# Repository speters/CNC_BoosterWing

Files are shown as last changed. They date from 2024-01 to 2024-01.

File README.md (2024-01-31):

# grblHAL BoosterWing

A breakout board for the Texas Instruments EK-TM4C1294XL Launchpad running the [grblHAL TM4C1294](https://github.com/grblHAL/TM4C1294) firmware by [Terje Io](https://github.com/terjeio).

This is a Frankenstein style child of [GRBLHAL2000](https://github.com/Expatria-Technologies/grblhal_2000_PrintNC) and 
[CNC_Boosterpack](https://github.com/terjeio/CNC_Boosterpack).

There were two objectives for this:
  1. follow known-working proven schematics - no questions asked
  2. keep it manufacturable by JLCPCB with the least costs for extended parts

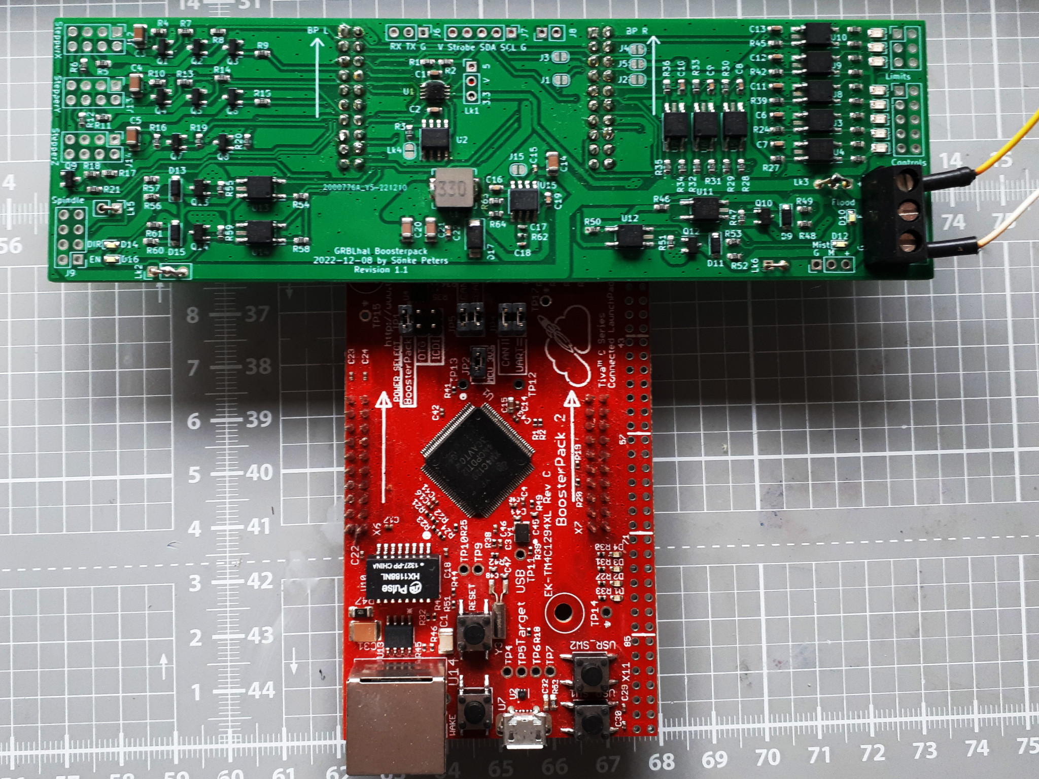
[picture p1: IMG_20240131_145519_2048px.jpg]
photo of BoosterWing with TM4C1294 board


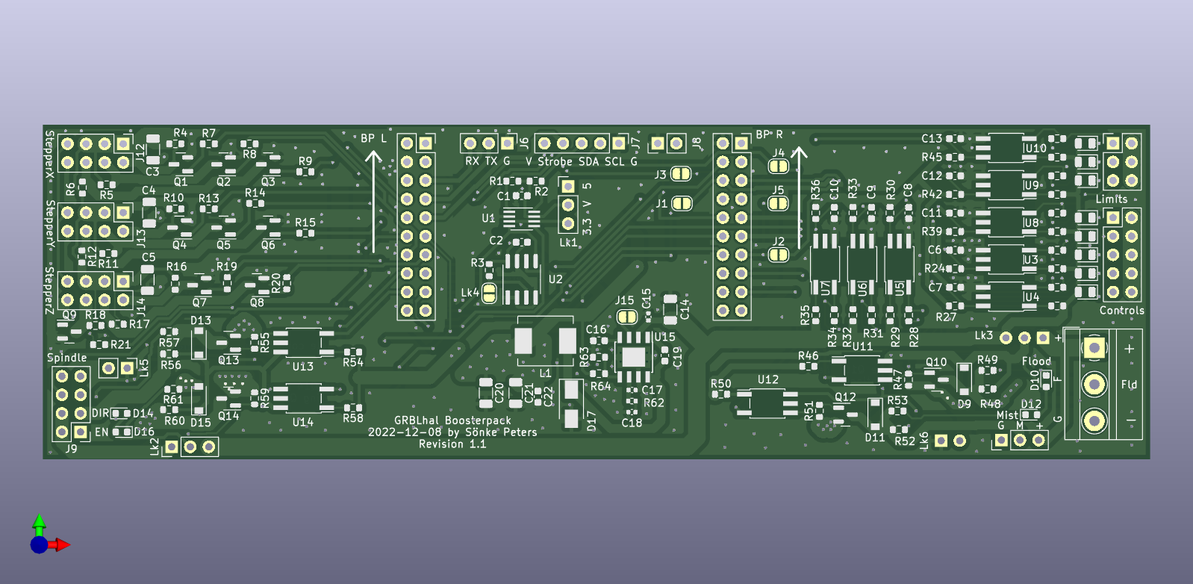
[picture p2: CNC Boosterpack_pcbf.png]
PCB front


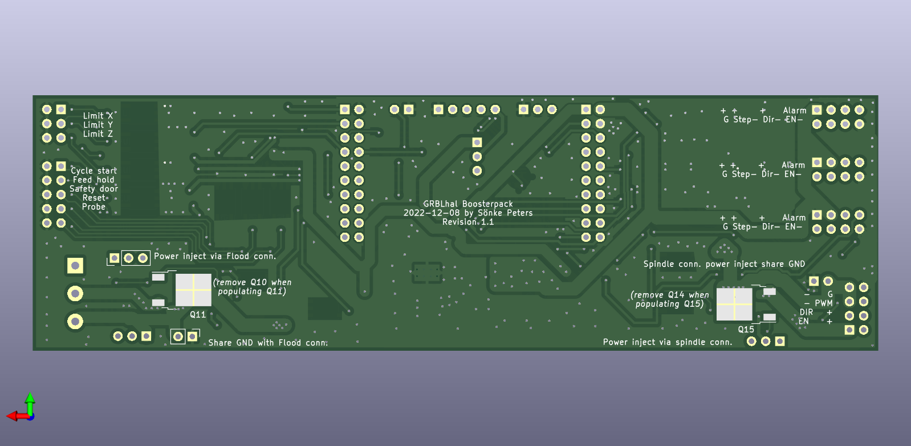
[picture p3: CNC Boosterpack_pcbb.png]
PCB back


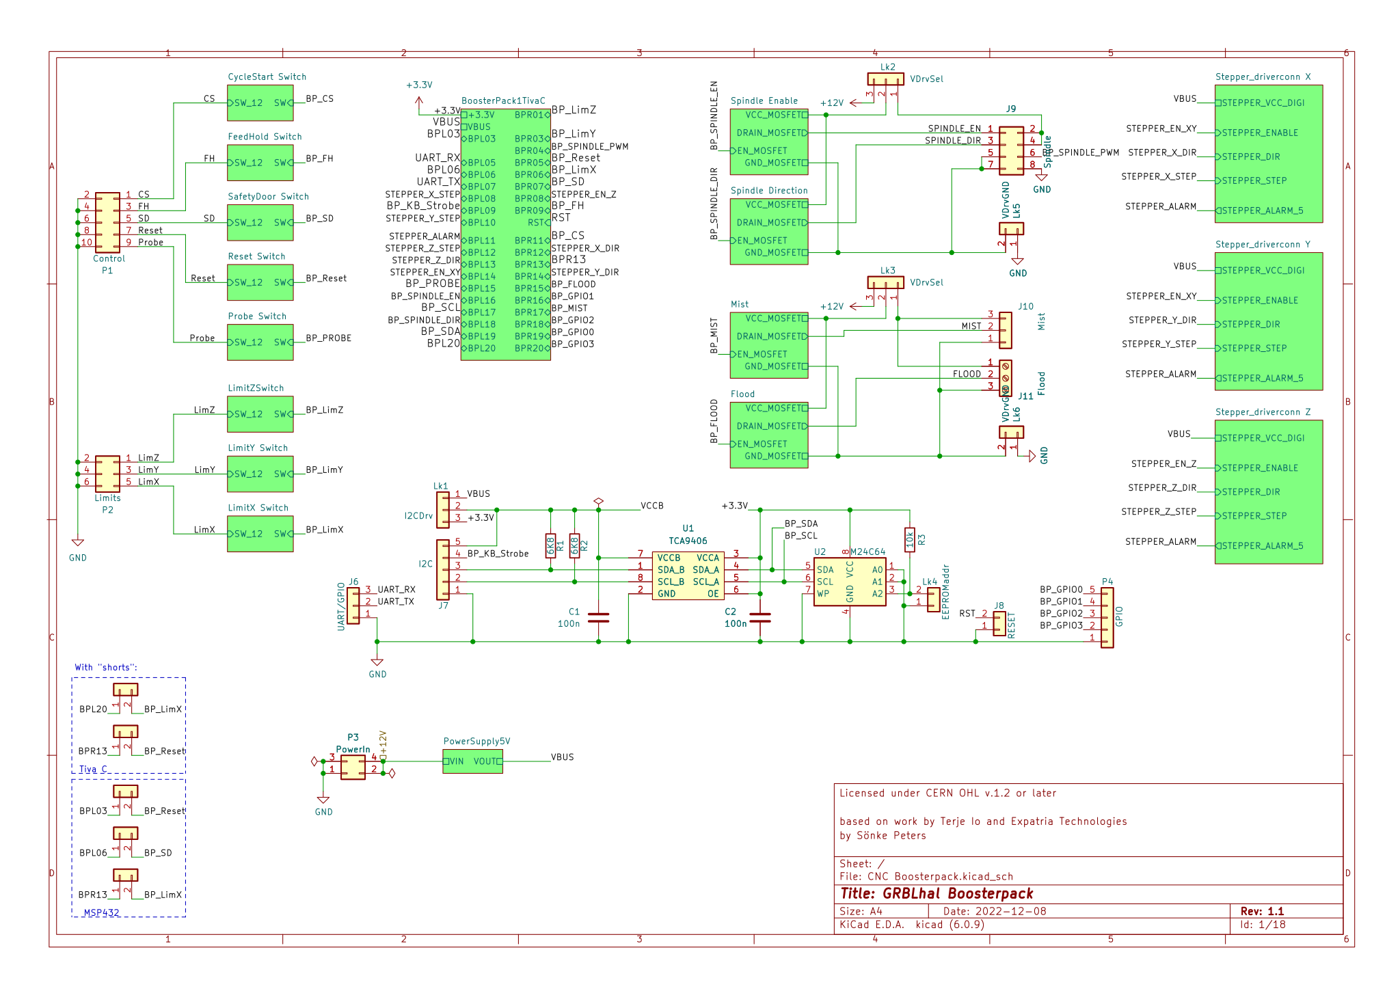
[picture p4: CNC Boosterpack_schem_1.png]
Schematics


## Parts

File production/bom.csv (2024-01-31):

Designator | Footprint | Quantity | Value | LCSC Part #
C1, C10, C11, C12, C13, C19, C2, C22, C6, C7, C8, C9 | C_0603_1608Metric | 12 | 100n | C14663
C14 | C_1206_3216Metric | 1 | 10u
C15 | C_0402_1005Metric | 1 | 10n
C16 | C_0603_1608Metric | 1 | 8.2n | C27920
C17 | C_0402_1005Metric | 1 | 10p | C32949
C18 | C_0402_1005Metric | 1 | 6.8n | C1542
C20, C21 | C_1206_3216Metric | 2 | 22u
C3, C4, C5 | C_1206_3216Metric | 3 | 22uF 10V | C5672
D1, D2, D3, D4, D5, D6, D7, D8 | LED_0805_2012Metric | 8 | LED y | C2296
D10, D12, D14, D16 | LED_0603_1608Metric | 4 | LED wt | C2290
D11, D13, D15, D9 | D_SOD-123 | 4 | B5819W SL | C8598
D17 | D_SMA | 1 | SS54
J1, J2, J3, J4, J5 | SolderJumper-2_P1.3mm_Open_RoundedPad1.0x1.5mm | 5 | 0
J10 | PinHeader_1x03_P2.54mm_Vertical | 1 | Mist
J11 | TerminalBlock_MetzConnect_Type011_RT05503HBWC_1x03_P5.00mm_Horizontal | 1 | Flood
J12, J13, J14 | PinHeader_2x04_P2.54mm_Vertical | 3 | StepperDrv
J15 | SolderJumper-2_P1.3mm_Open_RoundedPad1.0x1.5mm | 1 | 5V off
J6 | PinHeader_1x03_P2.54mm_Vertical | 1 | UART/GPIO
J7 | PinHeader_1x05_P2.54mm_Vertical | 1 | I2C
J8 | PinHeader_1x02_P2.54mm_Vertical | 1 | RESET
J9 | PinHeader_2x04_P2.54mm_Vertical | 1 | Spindle
L1 | L_Neosid_SM-PIC0602H | 1 | 33uH | C329385
Lk1 | PinHeader_1x03_P2.54mm_Vertical | 1 | I2CDrv
Lk2, Lk3 | PinHeader_1x03_P2.54mm_Vertical | 2 | VDrvSel
Lk4 | SolderJumper-2_P1.3mm_Open_RoundedPad1.0x1.5mm | 1 | EEPROMaddr
Lk5, Lk6 | PinHeader_1x02_P2.54mm_Vertical | 2 | VDrvGND
P1 | PinHeader_2x05_P2.54mm_Vertical | 1 | Control
P2 | PinHeader_2x03_P2.54mm_Vertical | 1 | Limits
P5 | PinSocket_2x10_P2.54mm_Vertical | 1 | BPConnL
P6 | PinSocket_2x10_P2.54mm_Vertical | 1 | BPConnR
Q1, Q2, Q3, Q4, Q5, Q6, Q7, Q8, Q9 | SOT-23 | 9 | MMBT5551 | C2145
Q10, Q12, Q13, Q14 | SOT-23 | 4 | AO3400A | C20917
R1, R2 | R_0603_1608Metric | 2 | 6K8 | C23212
R10, R11, R12, R16, R17, R18, R22, R25, R28, R31, R34, R37, R4, R40, R43, R5, R6 | R_0603_1608Metric | 17 | 4k7 | C23162
R13, R14, R15, R19, R20, R21, R23, R26, R29, R32, R35, R38, R41, R44, R7, R8, R9 | R_0603_1608Metric | 17 | 2k2 | C4190
R24, R27, R3, R30, R33, R36, R39, R42, R45, R63 | R_0603_1608Metric | 10 | 10k | C25804
R46, R50, R54, R58 | R_0603_1608Metric | 4 | 510 | C23193
R47, R51, R55, R59 | R_0603_1608Metric | 4 | 1k | C21190
R48, R49, R52, R53, R56, R57, R60, R61 | R_0603_1608Metric | 8 | 4,7k | C23162
R62 | R_0402_1005Metric | 1 | 51k | C25794
R64 | R_0603_1608Metric | 1 | 2k | C22975
U1 | SSOP-8_2.95x2.8mm_P0.65mm | 1 | TCA9406 | C337496
U10, U11, U12, U13, U14, U3, U4, U5, U6, U7, U8, U9 | SO-5_4.4x3.6mm_P1.27mm_fake | 12 | EL357N(B) | C6649
U15 | TI_SO-PowerPAD-8_ThermalVias | 1 | TPS54331DR | C9865
U2 | SOIC-8_3.9x4.9mm_P1.27mm | 1 | M24C64 | C79988

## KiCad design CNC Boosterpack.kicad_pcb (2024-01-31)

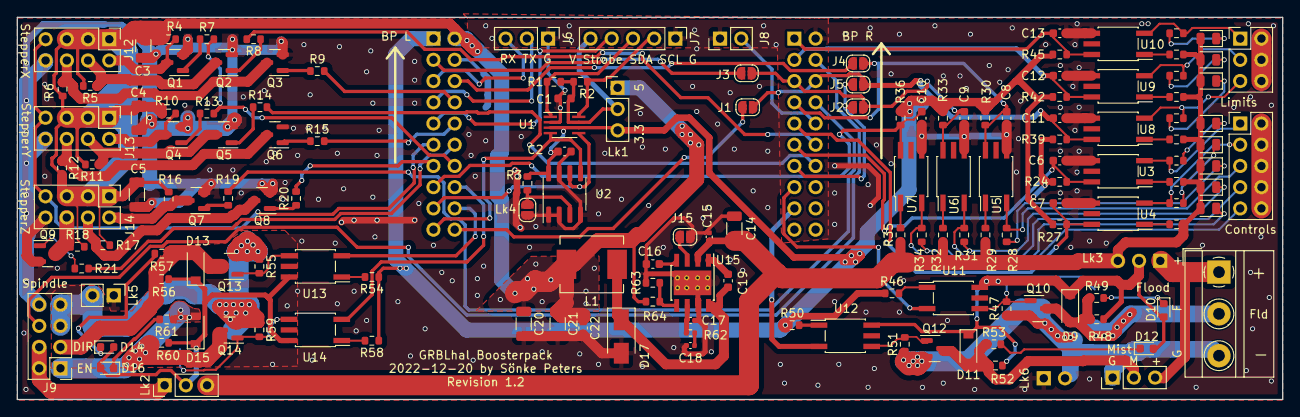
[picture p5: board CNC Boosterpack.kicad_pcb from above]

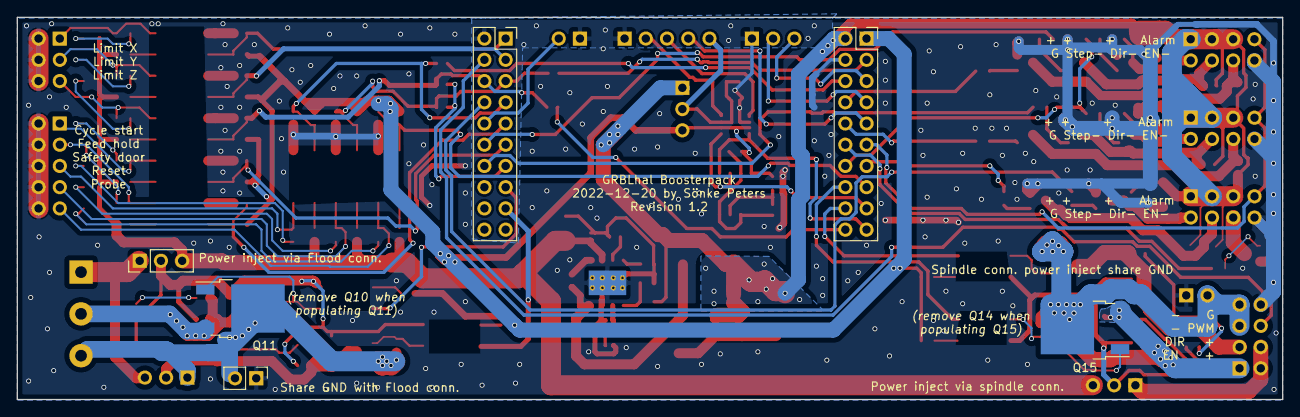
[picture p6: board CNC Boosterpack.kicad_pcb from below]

Board: 2 copper layers, 151.4 x 45.7 mm, 159 parts (6 on the bottom side), 111 nets.

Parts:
C1, C2, C6, C7, C8, C9, C10, C11, C12, C13, C19, C22: 100n; C_0603_1608Metric
C3, C4, C5: 22uF 10V; C_1206_3216Metric
C14: 10u; C_1206_3216Metric
C15: 10n; C_0402_1005Metric
C16: 8.2n; C_0603_1608Metric
C17: 10p; C_0402_1005Metric
C18: 6.8n; C_0402_1005Metric
C20, C21: 22u; C_1206_3216Metric
D1, D2, D3, D4, D5, D6, D7, D8: LED y; LED_0805_2012Metric
D9, D11, D13, D15: B5819W SL; D_SOD-123
D10, D12, D14, D16: LED wt; LED_0603_1608Metric
D17: SS54; D_SMA
J1, J2, J3, J4, J5: 0; SolderJumper-2_P1.3mm_Open_RoundedPad1.0x1.5mm
J6: UART/GPIO; PinHeader_1x03_P2.54mm_Vertical
J7: I2C; PinHeader_1x05_P2.54mm_Vertical
J8: RESET; PinHeader_1x02_P2.54mm_Vertical
J9: Spindle; PinHeader_2x04_P2.54mm_Vertical
J10: Mist; PinHeader_1x03_P2.54mm_Vertical
J11: Flood; TerminalBlock_MetzConnect_Type011_RT05503HBWC_1x03_P5.00mm_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
J12, J13, J14: StepperDrv; PinHeader_2x04_P2.54mm_Vertical
J15: 5V off; SolderJumper-2_P1.3mm_Open_RoundedPad1.0x1.5mm
L1: 33uH; L_Neosid_SM-PIC0602H
Lk1: I2CDrv; PinHeader_1x03_P2.54mm_Vertical
Lk2, Lk3: VDrvSel; PinHeader_1x03_P2.54mm_Vertical
Lk4: EEPROMaddr; SolderJumper-2_P1.3mm_Open_RoundedPad1.0x1.5mm
Lk5, Lk6: VDrvGND; PinHeader_1x02_P2.54mm_Vertical
P1: Control; PinHeader_2x05_P2.54mm_Vertical
P2: Limits; PinHeader_2x03_P2.54mm_Vertical
P5: BPConnL; PinSocket_2x10_P2.54mm_Vertical
P6: BPConnR; PinSocket_2x10_P2.54mm_Vertical
Q1, Q2, Q3, Q4, Q5, Q6, Q7, Q8, Q9: MMBT5551; SOT-23
Q10, Q12, Q13, Q14: AO3400A; SOT-23
Q11, Q15: HSU3016; TO-252-2
R1, R2: 6K8; R_0603_1608Metric
R3, R24, R27, R30, R33, R36, R39, R42, R45, R63: 10k; R_0603_1608Metric
R4, R5, R6, R10, R11, R12, R16, R17, R18, R22, R25, R28, R31, R34, R37, R40, R43: 4k7; R_0603_1608Metric
R7, R8, R9, R13, R14, R15, R19, R20, R21, R23, R26, R29, R32, R35, R38, R41, R44: 2k2; R_0603_1608Metric
R46, R50, R54, R58: 510; R_0603_1608Metric
R47, R51, R55, R59: 1k; R_0603_1608Metric
R48, R49, R52, R53, R56, R57, R60, R61: 4,7k; R_0603_1608Metric
R62: 51k; R_0402_1005Metric
R64: 2k; R_0603_1608Metric
U1: TCA9406; SSOP-8_2.95x2.8mm_P0.65mm
U2: M24C64; SOIC-8_3.9x4.9mm_P1.27mm
U3, U4, U5, U6, U7, U8, U9, U10, U11, U12, U13, U14: EL357N(B); SO-5_4.4x3.6mm_P1.27mm_fake
U15: TPS54331DR; TI_SO-PowerPAD-8_ThermalVias

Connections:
+3.3V: C2.1, Lk1.3, P5.1, R3.2, R24.2, R27.2, R30.2, R33.2, R36.2, R39.2, R42.2, R45.2, R46.1, R50.1, R54.1, R58.1, U1.3 (VCCA), U1.6 (OE), U2.8 (VCC)
+12V: C14.1, C15.1, D1.2 (A), D2.2 (A), D3.2 (A), D4.2 (A), D5.2 (A), D6.2 (A), D7.2 (A), D8.2 (A), Lk2.3, Lk3.3, R23.1, R26.1, R29.1, R32.1, R35.1, R38.1, R41.1, R44.1, U15.2 (VIN)
/BPL03: J3.1, P5.3
/BPL06: J4.1, P5.6
/BPL20: J1.1, P5.20
/BPR13: J2.1, J5.1, P6.13
/BP_CS: C6.1, P6.11, R24.1, U3.4
/BP_FH: C7.1, P6.9, R27.1, U4.4
/BP_FLOOD: P6.15, U11.2
/BP_KB_Strobe: J7.4, P5.9
/BP_LimX: C11.1, J1.2, J5.2, P6.6, R39.1, U8.4
/BP_LimY: C12.1, P6.3, R42.1, U9.4
/BP_LimZ: C13.1, P6.1, R45.1, U10.4
/BP_MIST: P6.17, U12.2
/BP_PROBE: C10.1, P5.15, R36.1, U7.4
/BP_Reset: C9.1, J2.2, J3.2, P6.5, R33.1, U6.4
/BP_SCL: P5.17, U1.5 (SCL_A), U2.6 (SCL)
/BP_SD: C8.1, J4.2, P6.7, R30.1, U5.4
/BP_SDA: P5.19, U1.4 (SDA_A), U2.5 (SDA)
/BP_SPINDLE_DIR: P5.18, U13.2
/BP_SPINDLE_EN: P5.16, U14.2
/BP_SPINDLE_PWM: J9.6, P6.4
/CS: P1.1, R22.1, U3.2
/FH: P1.3, R25.1, U4.2
/FLOOD: D9.2 (A), J11.2, Q10.3 (D), Q11.3 (D), R48.1, R49.1
/Flood/GND_MOSFET: J10.1, J11.3, Lk6.2, Q10.2 (S), Q11.2 (S), Q12.2 (S), R47.1, R51.1
/Flood/VCC_MOSFET: D9.1 (K), D10.2 (A), D11.1 (K), D12.2 (A), Lk3.2, R48.2, R52.2, U11.4, U12.4
/LimX: P2.5, R37.1, U8.2
/LimY: P2.3, R40.1, U9.2
/LimZ: P2.1, R43.1, U10.2
/MIST: D11.2 (A), J10.2, Q12.3 (D), R52.1, R53.1
/Probe: P1.9, R34.1, U7.2
/RST: J8.2, P6.10
/Reset: P1.7, R31.1, U6.2
/SD: P1.5, R28.1, U5.2
/SPINDLE_DIR: D13.2 (A), J9.3, Q13.3 (D), R56.1, R57.1
/SPINDLE_EN: D15.2 (A), J9.1, Q14.3 (D), Q15.3 (D), R60.1, R61.1
/STEPPER_ALARM: J12.7, J13.7, J14.7, P5.11
/STEPPER_EN_XY: P5.14, R7.2, R13.2
/STEPPER_EN_Z: P6.8, R19.2
/STEPPER_X_DIR: P6.12, R8.2
/STEPPER_X_STEP: P5.8, R9.2
/STEPPER_Y_DIR: P6.14, R14.2
/STEPPER_Y_STEP: P5.10, R15.2
/STEPPER_Z_DIR: P5.13, R20.2
/STEPPER_Z_STEP: P5.12, R21.2
/Spindle Direction/GND_MOSFET: J9.5, J9.7, Lk5.2, Q13.2 (S), Q14.2 (S), Q15.2 (S), R55.1, R59.1
/Spindle Direction/VCC_MOSFET: D13.1 (K), D14.2 (A), D15.1 (K), D16.2 (A), Lk2.2, R56.2, R60.2, U13.4, U14.4
/Stepper_driverconn X/DIR-: J12.4, Q2.3 (C), R5.1
/Stepper_driverconn X/EN-: J12.2, Q1.3 (C), R4.1
/Stepper_driverconn X/STEP-: J12.6, Q3.3 (C), R6.1
/Stepper_driverconn Y/DIR-: J13.4, Q5.3 (C), R11.1
/Stepper_driverconn Y/EN-: J13.2, Q4.3 (C), R10.1
/Stepper_driverconn Y/STEP-: J13.6, Q6.3 (C), R12.1
/Stepper_driverconn Z/DIR-: J14.4, Q8.3 (C), R17.1
/Stepper_driverconn Z/EN-: J14.2, Q7.3 (C), R16.1
/Stepper_driverconn Z/STEP-: J14.6, Q9.3 (C), R18.1
/UART_RX: J6.3, P5.5
/UART_TX: J6.2, P5.7
/VBUS: C3.1, C4.1, C5.1, C20.1, C21.1, C22.1, J12.1, J12.3, J12.5, J13.1, J13.3, J13.5, J14.1, J14.3, J14.5, L1.2, Lk1.1, P5.2, R4.2, R5.2, R6.2, R10.2, R11.2, R12.2, R16.2, R17.2, R18.2, R63.1
/VCCB: C1.1, J7.5, Lk1.2, R1.1, R2.1, U1.7 (VCCB)
GND: C1.2, C2.2, C3.2, C4.2, C5.2, C6.2, C7.2, C8.2, C9.2, C10.2, C11.2, C12.2, C13.2, C14.2, C15.2, C16.2, C17.2, C18.2, C20.2, C21.2, C22.2, D17.2 (A), J6.1, J7.1, J8.1, J9.8, J12.8, J13.8, J14.8, J15.1, Lk4.1, Lk5.1, Lk6.1, P1.2, P1.4, P1.6, P1.8, P1.10, P2.2, P2.4, P2.6, P5.4, P6.2, Q1.2 (E), Q2.2 (E), Q3.2 (E), Q4.2 (E), Q5.2 (E), Q6.2 (E), Q7.2 (E), Q8.2 (E), Q9.2 (E), R64.2, U1.2 (GND), U2.1 (A0), U2.2 (A1), U2.4 (GND), U2.7 (WP), U3.3, U4.3, U5.3, U6.3, U7.3, U8.3, U9.3, U10.3, U15.7 (GND), U15.9 (PAD)
unnamed: C16.1, U15.4 (SS)
unnamed: C17.1, R62.1, U15.6 (COMP)
unnamed: C18.1, R62.2
unnamed: C19.1, D17.1 (K), L1.1, U15.8 (PH)
unnamed: C19.2, U15.1 (BOOT)
unnamed: D1.1 (K), R22.2
unnamed: D2.1 (K), R25.2
unnamed: D3.1 (K), R28.2
unnamed: D4.1 (K), R31.2
unnamed: D5.1 (K), R34.2
unnamed: D6.1 (K), R37.2
unnamed: D7.1 (K), R40.2
unnamed: D8.1 (K), R43.2
unnamed: D10.1 (K), R49.2
unnamed: D12.1 (K), R53.2
unnamed: D14.1 (K), R57.2
unnamed: D16.1 (K), R61.2
unnamed: J7.2, R2.2, U1.8 (SCL_B)
unnamed: J7.3, R1.2, U1.1 (SDA_B)
unnamed: J9.2, J9.4, Lk2.1
unnamed: J10.3, J11.1, Lk3.1
unnamed: J15.2, U15.3 (EN)
unnamed: Lk4.2, R3.1, U2.3 (A2)
unnamed: Q1.1 (B), R7.1
unnamed: Q2.1 (B), R8.1
unnamed: Q3.1 (B), R9.1
unnamed: Q4.1 (B), R13.1
unnamed: Q5.1 (B), R14.1
unnamed: Q6.1 (B), R15.1
unnamed: Q7.1 (B), R19.1
unnamed: Q8.1 (B), R20.1
unnamed: Q9.1 (B), R21.1
unnamed: Q10.1 (G), Q11.1 (G), R47.2, U11.3
unnamed: Q12.1 (G), R51.2, U12.3
unnamed: Q13.1 (G), R55.2, U13.3
unnamed: Q14.1 (G), Q15.1 (G), R59.2, U14.3
unnamed: R23.2, U3.1
unnamed: R26.2, U4.1
unnamed: R29.2, U5.1
unnamed: R32.2, U6.1
unnamed: R35.2, U7.1
unnamed: R38.2, U8.1
unnamed: R41.2, U9.1
unnamed: R44.2, U10.1
unnamed: R46.2, U11.1
unnamed: R50.2, U12.1
unnamed: R54.2, U13.1
unnamed: R58.2, U14.1
unnamed: R63.2, R64.1, U15.5 (VSENSE)

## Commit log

2022-11-24 some part rotations, JLCPCB ordered #W202211241441380
    [CNC Boosterpack.kicad_sch, mosfet.kicad_sch, mosfet_2possibilities.kicad_sch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]
2024-01-31 added JLCPCB production files
    [bom.csv, designators.csv, positions.csv]

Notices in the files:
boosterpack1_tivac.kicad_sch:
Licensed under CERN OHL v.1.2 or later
